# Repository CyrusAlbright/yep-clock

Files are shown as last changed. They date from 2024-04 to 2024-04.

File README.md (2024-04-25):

# Introduction

This is my final project for ECE 180 at BSU. It's way beyond the scope of the class, but the class is an intro class and I've already got plenty of experience working with electronics and programming, so I chose this mostly just to flex. The bulk of this project focuses on controlling several stepper motors simultaneously from an Arduino microcontroller. Essentially, this is a digital clock that, instead of using an LED or LCD display, uses physically rotating barrels, each of which displays one digit. Furthermore, I wanted to use the limitation that I would use no premade code, including libraries. Everything in this project was done by yours truly.

# Motivation

When brainstorming, one of the many ideas I came up with was inspired by my love for chess. In much of competitive and casual chess, a so-called "chess clock" is used, limiting the total amount of time a player can use to make their moves. But a normal digital clock is pretty easy to make and uninteresting, as it has been already done and mass-produced before in many different forms. In a similar vein to slot machines or the counters that track how many people leave an amusement park ride, I wanted to make a physical display that uses rotating barrels with digits on them.

# Design overview

When workshopping the idea, I had to figure out what all would be needed. At the start of the project, I figured that I would essentially only need 4 motors and some way to control them all. I settled on using stepper motors and shift registers. The final schematic can be seen below:

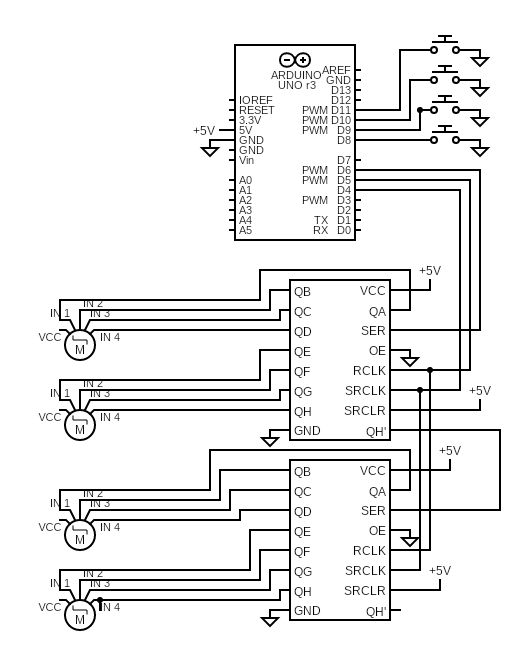
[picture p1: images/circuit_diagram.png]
Circuit diagram


## Component choice

### Motors

I settled upon the 28byj-48 stepper motor, a small cheap 4-phase stepper. Before starting this project, it seemed like the ideal choice because it can work on 5V (which the Arduino Uno uses), it is small and inexpensive, and I can precisely control the output angle. Typical DC motors just spin with an applied voltage, and so I would have to somehow measure how fast and far it moved and compensate, so DC motors didn't seem like a correct choice. Using servos would be a good idea, as those can achieve precise control and be fairly quick. However, I couldn't find a reasonable servo that could also do a "full continuous rotation" where there were no endstops.

If I revisit this project, finding a small, lightweight, and fast motor whose position can be precisely measured and controlled will be imperative. The steppers work somewhat, but with a faster rotational speed I would be able to implement the full goal of the project. This is explored more in the Limitations portion of the writeup down below.

These steppers came with driver modules, essentially just Darlington transistor arrays with flyback diodes to damp feedback spikes from switching the motor coils off. The Darlington transistors allow a much larger current (~100mA at 5V to run the coils) to be controlled by a small current (the Arduino output pins can't handle much load at all, max of around ~20mA). These driver modules have 2 power pins for 5V in and 4 control pins, one for each separate coil.

### Shift registers

As the motors I chose required 4 pins to control, if I were to drive them all directly from the Arduino, I would need 16 output pins, which would not work. Therefore, I needed a shift register, which would allow me to control several parallel output pins using only a few (3) serial inputs. I already had a 74HC595 shift register on hand, but that could only run 8 total output pins. I bought more and chained 2 together to give me a 16 pin shift register, allowing me to drive all the motors. This would require more code complexity and slightly limit what was possible, but would greatly reduce and simplify the wiring problem I would otherwise have.

# Programming

Programming everything was by far the hardest part of this project. I'll break it down by sequentially increasing difficulty.

## Driving a single stepper at constant continuous rotation

First, I got a proof of concept working, driving a single stepper motor from the Arduino's output pins. There are 4 pins for driving the motor, each corresponding to a single coil, and they need to be driven in a specific order to get proper stepping action. Otherwise, it would vibrate in place or do nothing. I used full-step mode, as that would be easiest to implement, where each coil is toggled between fully-on and fully-off. I won't go too much into the details of the coil activation sequences, as there are a variety of online guides that explain this in the proper depth with helpful illustrations.

## Expanding the available output ports using a shift register

After getting a single motor driven from the Arduino's output pins, I needed to figure out how to work the shift register. I started by breadboarding everything and connecting the output pins of the shift register to LEDs with series resistors to ground, then connecting the 5V and ground pins, then the serial input and clock and latch inputs to the Arduino's output pins, then writing some code that would write out certain combinations to the shift register by pulsing the serial pins with the data, pulsing the clock pin once per data bit, and toggling the latch pin at the beginning and end of a sequence.

### Resolving floating pins

To my surprise, everything worked the first time, mostly. However, I had a strange issue where if my hand got too close or too far away from the breadboard, it would shift between working and not working. There had to be a floating pin somewhere in the circuit, where an input pin is disconnected from anything and stray charges from the surrounding environment can cause it to appear as either on or off. I then checked the data sheet for the shift register again and found that the inverted output enable pin and the inverted clear pin in my circuit needed to be tied to ground and +5V respectively. This solved that issue. With that working, I was able to remove the LEDs from the circuit and hook up the output from the shift register to the steppers.

## Driving multiple motors at constant continuous rotation

Then I needed to resolve the issue of driving more than one stepper at the same time. At that time, my code was pretty much "pulse the proper coils for the current step, wait 5ms, adjust the current step, repeat." This represented a constant rotation in a single direction for a single motor. At first, I just modified this code to drive all the steppers to the same rotation, just to make sure everything worked. 

## Driving multiple motors with independent rotations using state machines

Then I added controls for turning the rotation on and off, then separate counters for current step and desired step, then a state machine-based implementation that handles scheduling, bidirectional drive, and "manual PWM" to reduce the current and avoid saturating the motor coils (which wastes energy and risks damaging the motors via heat). The final implementation is fairly elegant and idiomatic C if I say so myself. To change the position of the motors, all that needs to be done is to adjust the desired position of that motor, and the state machine handler essentially does the rest, calculating if it needs to move, in which direction it needs to move, and using the current time and given tick times to schedule an on-off PWM signal for each of the 4 coils per motor.

My state machine handler was specifically designed to be non-blocking (see https://en.wikipedia.org/wiki/Blocking_(computing)). In terms of what this means, essentially it allows other operations to be done during the same time period. In the initial implementation, the code was completely blocking, spending 5ms with the coils in one state, then 5ms with the coils in another state. If any other code needed to be run during that time frame, it would have to work around the fact that there would be 5ms between successive runs. In a non-blocking style, any number of non-blocking components can be combined without having to wait for these activations to be done. This is called cooperative multitasking, and is essentially a way to pretend to have multiple threads of execution on a single-threaded system.

My implementation is extensible enough that I would easily be able to drive several more motors if I wanted to. The computation time per loop spent on calculating which coils need to be activated is pretty negligible, so scaling upwards to e.g. controlling 20 steppers at a time pretty much boils down to properly setting up the StepperConfiguration array and then just adjusting the shift register handling code to shift out however many bits are needed. Power's not even that much of an issue, as hardly ever is more than one stepper motor active at a time, and they each draw around 500 mW when active. Most good USB power supplies nowadays can handle 5V at 1A easily, sometimes even to 3A. 

As always, I have gripes with using C/C++ because it's old, fairly unergonomic, and easy to shoot yourself in the foot with. I much prefer languages with a more flexible type system. For instance, using Rust, I could easily model the state machine as a sum type, thereby giving more type safety (e.g. avoiding invalid states) and simplifying the program logic. In practice, since this implementation is fairly straightforward, C/C++ is okay, but in a more complicated situation, with more states and more complicated logic, the state machine would be much harder to debug in C/C++. I am of course biased towards Rust, and I have previously experimented with running Rust on the Arduino platform, but I wanted to make a complete project using C/C++ so that I could better understand it.

# Printed parts

I didn't have too much time to work on this part, so I got only the strictly necessary parts done, that being the barrels with the digits on them. I modeled a 5 cm diameter barrel in Fusion with a cutout matching the contour of the stepper motor's shaft. Then I needed to get the text wrapping around the outside. Fusion didn't have good support for this, so I imported the model into Blender and found out how to do it there. Unfortunately, neither program really does curved text well. In the final model, the embossed text is glitchy. In any case, they're included in the /models/ folder if you want to experiment.

# Limitations

I eventually realized that due to the limitations of the stepper motors I used, the concept of a chess clock using stepper motors was unviable due to many chess time controls using increment, where a certain amount of time is added to your clock per move. This would require a lot of fast rotation on the part of the ones digit of the seconds, and the steppers I chose can only handle a max of around 10 revolutions per minute, or ~0.16 revolutions per second. Given that many common chess time formats have 2 to 10 second increment per move, the stepper showing the ones digit of the seconds would not have enough time to catch up and so the display would lag noticeably behind which is extremely undesirable especially when a player's remaining time is running low.

I might be able to make it work with the steppers by using some kind of gearing system to increase rotational speed, but I'm not a mechanical engineer and am not particularly interested in going down that route anyway. Maybe I could use a magnetic hall effect sensor to measure angle in combination with a brushless DC motor with some kind of closed loop feedback system. It's something to look into anyway.

In practice, for this project, I'm just counting minutes and seconds upward from when it's plugged in. Not as interesting or useful, but it's a proof of concept that might be revisited.

# Conclusion

I learned a lot about motor control both in the pre-project research and during the course of implementing it. I think that there's a good market for inexpensive motor control boards (especially in the CNC and 3D printing world), and it's something I'd like to pursue further in the future, possibly looking into using other motor types as well. If or when I take an IC design course, encoding my state machine logic into a hardware implementation could be a good project, with possible improvements for handling half-stepping or microstepping.

Since in my initial motivation I wanted to make a chess clock and realized it wasn't possible due to the steppers being too slow, I would love to use a brushless DC motor and magnetic hall effect sensor in a closed loop system to get quick snappy movement that would make the project really shine and would be at home in a real chess tournament. With proper motor choice and design (both electrical and mechanical), I think it could be a stylish competitor to current digital chess clocks and could be much easier and more pleasant to read than the existing poor-contrast LCD chess clocks on the market, with the tradeoff of a much greater price point considering that good motors are not cheap. Alternately, a split-flap style design would probably be cheaper and easier to implement.

Another option is to drive the whole system using a single motor, and have a mechanical gearing and carry system, so that by controlling only the ones digit of the seconds, the entire display could update off of that. However, as mentioned before, I am not a mechanical engineer nor am I interested in that kind of work. It is possible that it could be simpler from a software perspective and less expensive due to using fewer motors, however it could possibly be less robust due to having more moving parts (if using 3D printed parts as I did for mine), and furthermore can only be used in "count up" or "count down" applications where there's only one digit that's truly independent and all the others can be driven by its movement.

This was ultimately a good project for learning about the control process and limitations of motors, and for learning about how to write robust C code. I wouldn't necessarily recommend it for beginners, as it's fairly easy to either destroy your Arduino board by drawing too much current from its pins or destroy the motors by leaving the same coils activated for too long and burning them, and furthermore my C code is fairly sophisticated and not easy to explain to somebody who hasn't used C before.

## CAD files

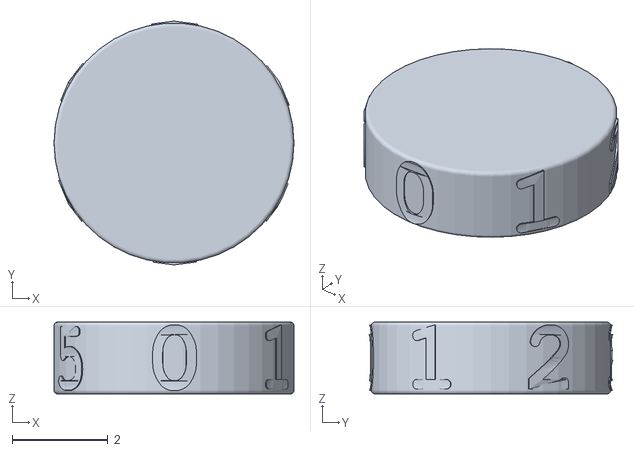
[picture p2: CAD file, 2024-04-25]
models/barrel6.stl
5.00 x 5.08 x 1.50

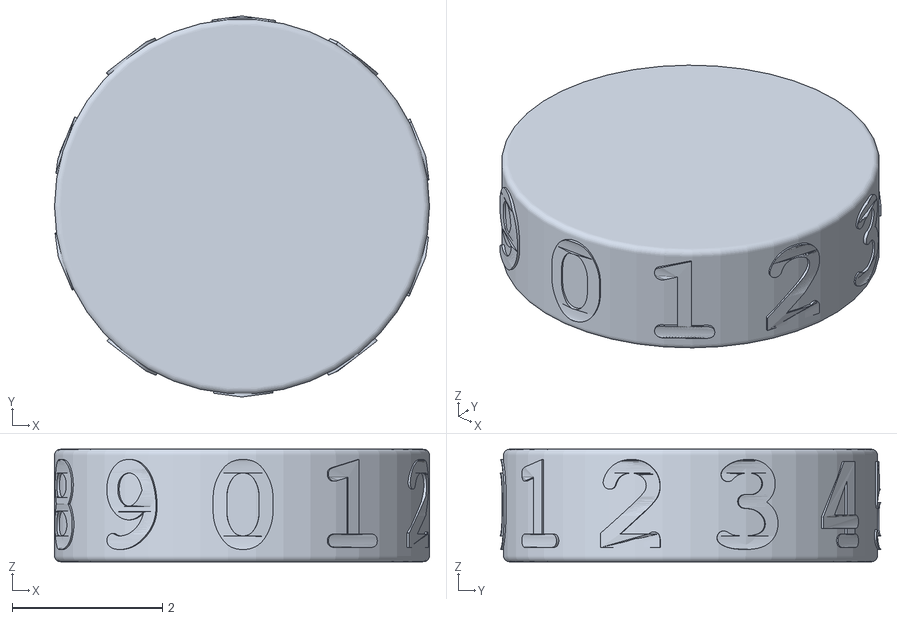
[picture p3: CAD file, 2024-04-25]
models/barrel10.stl
5.00 x 5.08 x 1.50

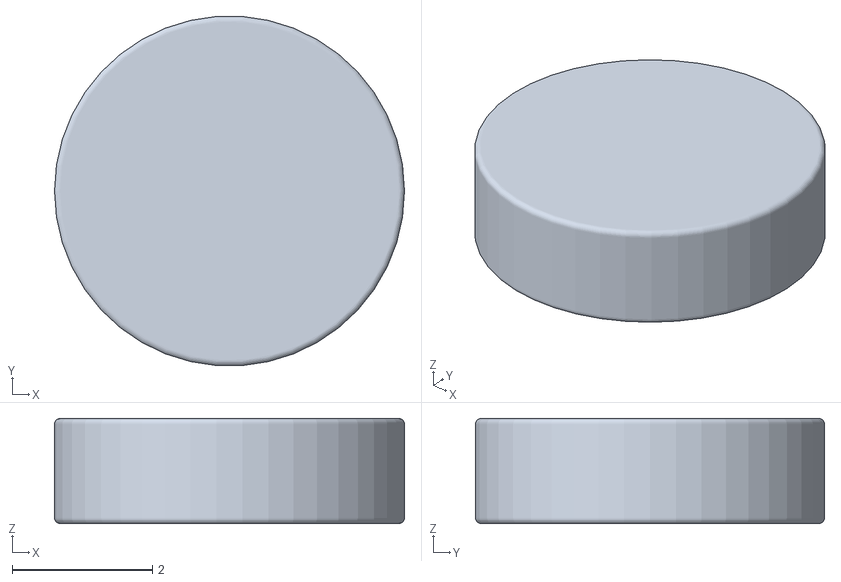
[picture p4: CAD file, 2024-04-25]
models/barrel_blank.obj
5.00 x 4.99 x 1.50

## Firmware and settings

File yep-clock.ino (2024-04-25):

// Further comments are in the included header files

#include "utils.h"
#include "state_machine.h"

// The amount of steps per revolution for the 28byj-48 stepper motor
constexpr uint32_t TOTAL_STEPS = 2048;

// Controls for the shift register
uint32_t data_pin = 4;
uint32_t clock_pin = 5;
uint32_t latch_pin = 6;

// All the information needed for a single stepper motor
typedef struct {
	int32_t desired_step;
	int32_t current_step;
	// on startup, the program has no way of knowing the current angle of the stepper motor
	// offset is a variable that can be manually adjusted so that the program's 0 can match the physical 0
	int32_t offset;
	StateMachine state_machine;
} StepperConfiguration;

// The "clock face" display
typedef struct {
	uint8_t minutes_tens;
	uint8_t minutes_ones;
	uint8_t seconds_tens;
	uint8_t seconds_ones;
} Display;

// All the motors to be used
StepperConfiguration steppers[] = {
	{0, 0, 0, {Idle, 0, 5, 2}},
	{0, 0, 0, {Idle, 0, 5, 2}},
	{0, 0, 0, {Idle, 0, 5, 2}},
	{0, 0, 0, {Idle, 0, 3, 1}}
};

Display current_display = {0, 0, 0, 0};
Display previous_display = current_display;

void setup() {
	pinMode(data_pin, OUTPUT);
	pinMode(clock_pin, OUTPUT);
	pinMode(latch_pin, OUTPUT);

	// Input buttons for manually adjusting the offset
	for (uint8_t i = 0; i < 4; i++) {
		pinMode(8 + i, INPUT_PULLUP);
	}
}

void loop() {
	uint32_t now = millis();

	current_display = display_from_time(now);
	
	// Only do potentially costly floating point operations once whenever the display face needs to change
	// Probably not a necessary optimization but it's low hanging fruit
	if (!display_equals(previous_display, current_display)) {
		auto d = current_display;
		steppers[0].desired_step = (float)(d.minutes_tens) * (float)(TOTAL_STEPS) / 6.0f;
		steppers[1].desired_step = (float)(d.minutes_ones) * (float)(TOTAL_STEPS) / 10.0f;
		steppers[2].desired_step = (float)(d.seconds_tens) * (float)(TOTAL_STEPS) / 6.0f;
		steppers[3].desired_step = ((float)(10 * (d.seconds_tens % 2)) + (float)(d.seconds_ones)) * (float)(TOTAL_STEPS) / 20.0f;
	}

	uint32_t coil_activations = 0;
	for (uint8_t i = 0; i < 4; i++) {
		auto stepper = steppers + i;

		// Get the normalized difference between the current and desired position
		// angle_diff is needed so that if the current position is at 359 degrees and it wants to go to 0 degrees it only needs to move 1 step instead of 359 steps
		// Putting angle_diff through unit_dir tells us a single step in which direction, or none at all
		auto angle = angle_diff(stepper->current_step, stepper->desired_step + stepper->offset, TOTAL_STEPS);
		auto unit_dir = unit_direction(angle);
		auto output = state_machine_tick(&stepper->state_machine, {now, unit_dir});
		stepper->current_step += output.steps_increment;
		auto this_stepper_coils = output.activate_coils ? step_to_coils(stepper->current_step) : 0;
		
		// Concatenate all the output bits into a single "bit array"
		coil_activations |= this_stepper_coils << (4 * (3 - i));
	}

	// Send the bit array to the shift register
	sendOut(coil_activations);

	// Manual control of offsets using the buttons
	bool buttons[4];
	for (uint8_t i = 0; i < 4; i++) {
		buttons[i] = !digitalRead(8 + i);
		steppers[i].offset += buttons[i];
	}

	previous_display = current_display;

	delayMicroseconds(10);
}

bool display_equals(Display a, Display b) {
	return
		a.minutes_tens == b.minutes_tens &&
		a.minutes_ones == b.minutes_ones &&
		a.seconds_tens == b.seconds_tens &&
		a.seconds_ones == b.seconds_ones;
}

Display display_from_time(Time now) {
	uint32_t s = now / 1000;
	uint8_t minutes = s / 60;
	uint8_t seconds = s % 60;

	uint8_t minutes_tens = minutes / 10;
	uint8_t minutes_ones = minutes % 10;
	uint8_t seconds_tens = seconds / 10;
	uint8_t seconds_ones = seconds % 10;

	return { minutes_tens, minutes_ones, seconds_tens, seconds_ones };
}

// The order of coil activations matters in terms of what direction the stepper will move
uint8_t step_to_coils(int32_t step) {
	switch (mod(step, 4)) {
		case 0:
			return 0b1001;
		case 1:
			return 0b1100;
		case 2:
			return 0b0110;
		case 3:
			return 0b0011;
	}
}

// For controlling the shift register
void sendOut(uint16_t output) {
	digitalWrite(latch_pin, LOW);
	shiftOut(data_pin, clock_pin, MSBFIRST, (uint8_t) (output >> 8));
	shiftOut(data_pin, clock_pin, MSBFIRST, (uint8_t) (output));
	digitalWrite(latch_pin, HIGH);
}

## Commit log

2024-04-25 Fix name, comment code
    [yep-clock.ino]
2024-04-25 Comment code, add models and circuit diagram
    [barrel10.stl, barrel6.stl, barrel_blank.obj]
